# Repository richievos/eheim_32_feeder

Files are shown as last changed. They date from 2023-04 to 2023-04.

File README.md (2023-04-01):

# Eheim ESP32 Feeder
This is used to convert an Eheim feeder to be powered by an ESP32. All the
Eheim parts were replaced with an ESP32.

Why? The primary reason is because I was trying to do a mod to my feeder and I
completely shorted out all the electronics. Since I have a variety of ESP style
microcontrollers on hand, I swapped out the insides and just kept the motor and
body parts.

put_together

## Parts

Pieces:
* Eheim autofeeder ([example](https://www.amazon.com/Everyday-Feeder-Programmable-Automatic-Dispenser/dp/B001F2117I/))
* One ESP32 controller ([example](https://www.amazon.com/gp/product/B0B764963C/)
* One USB cord
* One transistor eg a 2N3904 ([example kit](https://www.amazon.com/dp/B07G46LNCG))

## Wiring instructions

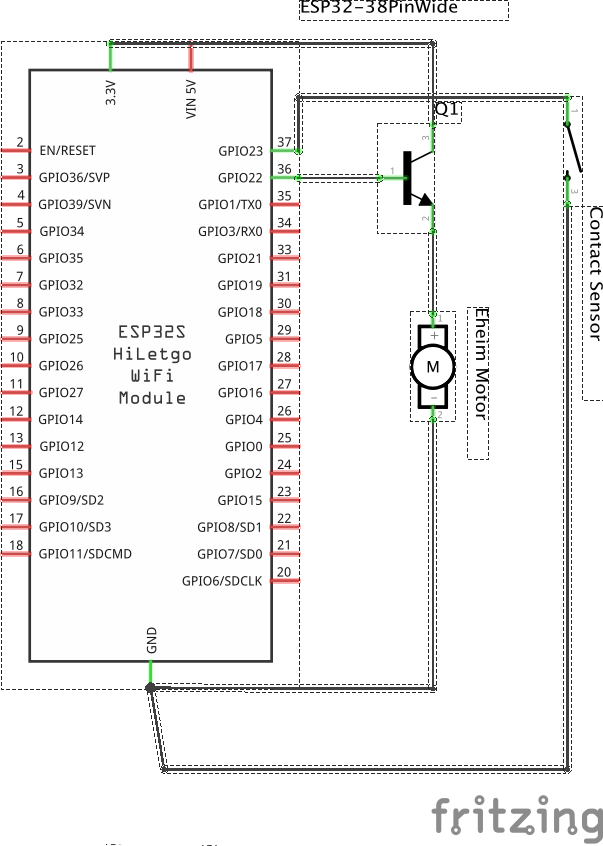
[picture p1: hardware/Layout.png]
hardware layout


**Motor and transistor:**
The motor has 2 wires, red and black.

* Black motor wire => any ground pin on the ESP32
* Transistor -- this sends 3.3V to the motor, controlled on/off by the ESP32:
    * _collector_ leg => the 3.3V output on the ESP32 (5V output likely works too)
    * _base_ leg => GPIO 22 on the ESP32 (`motorPins.powerOuput` in main.cpp)
    * _emitter_ leg => the motor's red wire

**Rotation Sensor**:
The rotation sensor also has 2 wires (red and black). This sensor is how we tell a rotation finished.

* Black sensor wire => any ground pin on the ESP32
* Red sensor wire => GPIO 23 on the ESP32 (`rotationSensorPins.input` in main.cpp)

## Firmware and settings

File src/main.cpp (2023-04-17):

#include <Arduino.h>
#include <NTPClient.h>

#include "feeder.h"
#include "mqtt.h"
#include "mywifi.h"
#include "ntp.h"
#include "ota.h"
#include "controller.h"

// pull in all the inputs last to make sure they're only being referenced from here
#include "inputs.h"

namespace feeder {
/*******************************
 * Shared vars
 *******************************/
MqttBroker mqttBroker(MQTT_BROKER_PORT);
MqttClient mqttClient(&mqttBroker);

std::shared_ptr<NTPClient> timeClient;

RotationSensorPins rotationSensorPins = {
    .input = 23};

MotorPins motorPins = {
    .powerOutput = 22};

void setup() {
    Serial.begin(115200);

    richiev::connectWifi(hostname, wifiSSID, wifiPassword);
    richiev::ota::setupOTA(hostname);

    // trigger a NTP refresh
    timeClient = std::move(ntp::setupNTP());

    controller::setupController(mqttBroker, mqttClient, timeClient);
    setupFeeder(rotationSensorPins, motorPins);
}

void loop() {
    const unsigned long loopStartedAt = timeClient->getEpochTime();
    loopFeeder(loopStartedAt);

    // Don't run this when the feeder is going, because this blocks and I
    // don't want networking to affect food being dumped in
    if (!isInFeed()) {
        richiev::mqtt::loopMQTT(mqttBroker, feeder::mqttClient);
        controller::loopController();

        ntp::loopNTP(timeClient);
        richiev::ota::loopOTA();
    }
}
}  // namespace feeder

void setup() { feeder::setup(); }
void loop() { feeder::loop(); }

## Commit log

2023-04-01 Add hardware fritz
    [Layout.fzz]
2023-04-06 Don't use timeClient for system logic
    I don't actually want the operations to use NTP based time because NTP based
    time can go backwards. That could cause all sorts of weirdness, even if it had
    logic to smooth the time roll-back.
    This logic really just cares about milliseconds of time having passed, not what
    that time is on external clocks. As such, it's more accurate to use millis.
    Interesting to reason through.
